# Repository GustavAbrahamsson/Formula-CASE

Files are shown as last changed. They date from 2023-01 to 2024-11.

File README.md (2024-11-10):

# Formula-CASE | Miniature Formula-style RC cars!

## ESP32-S3, FreeRTOS, 4WD
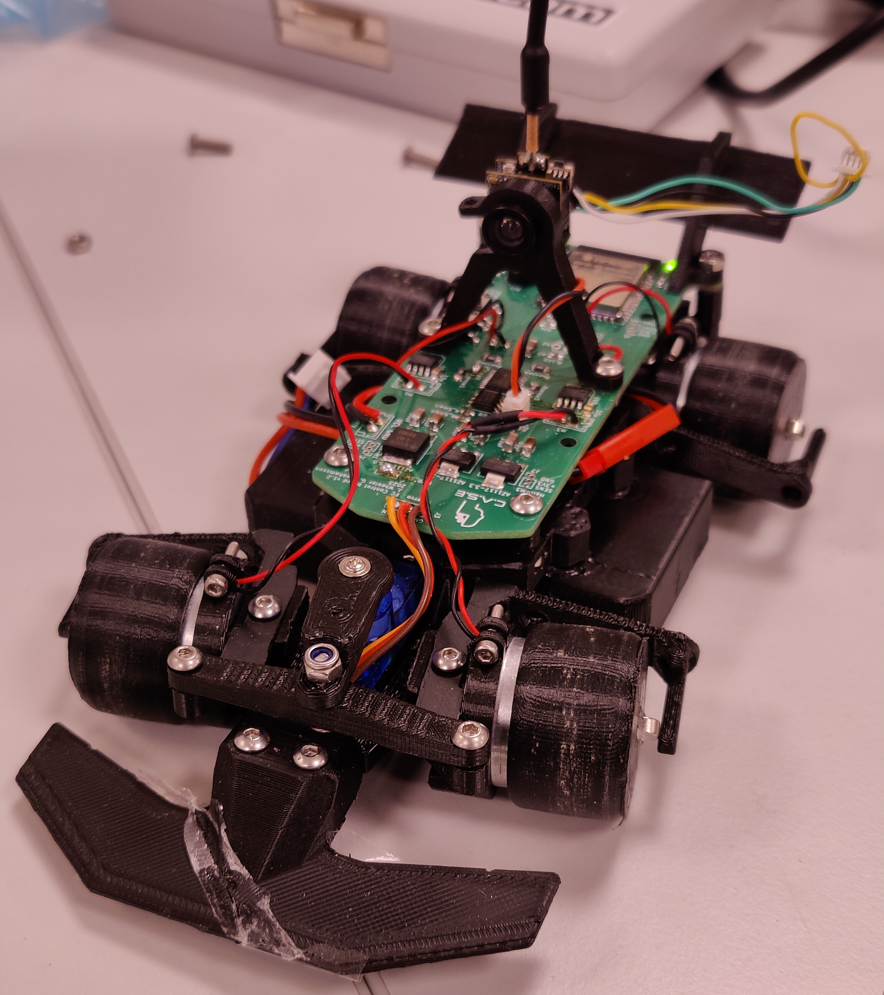
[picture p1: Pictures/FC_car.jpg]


## F1-inspired custom steering wheel, with magnetic paddle shifters


## Remote control with "driver POV" video feed


## PCB
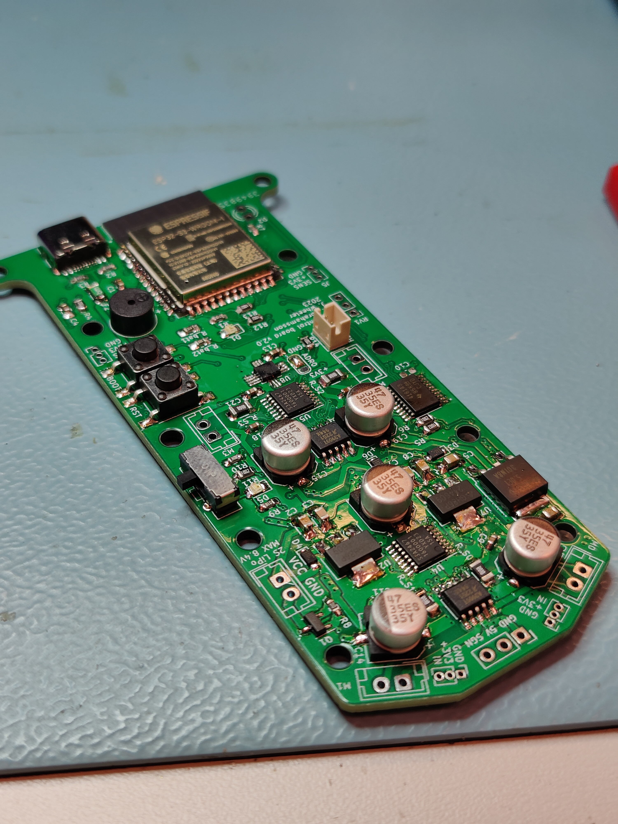
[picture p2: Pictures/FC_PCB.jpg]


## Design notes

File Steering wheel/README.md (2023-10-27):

# FC_Wheel PCB
## v1.0
### Issues:
- The pads for the ESP32-S3 footprint are too small 
- The ESP receives 2.4V even though the LDO outputs 3.3V
  - Use larger vias
- The BOOT and RESET push-buttons need to be more accessable and easier to press
  - Use 'longer' push-buttons with the same footprint
- The battery pins need labels
- The holes are not aligned for the MPU6050 footprint
- Cables
  - Move to a single PCB with no cables

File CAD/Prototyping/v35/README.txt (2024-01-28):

4 x Motor mount
6 x PCB_offset
2 x Rear_PCB_offset
2 x Wheel frame
2 x Wheel frame (mirrored)

1 x Everything else

Note:
2 x PCB_offset could also work

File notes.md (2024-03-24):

# Notes for FC-CONTROL_BOARD

## Hardware notes
### FC Control board v0.1
#### Known faults
- [ ] Wrong 3.3v regulator pinout ordered. Footprint is correct but non standard part was ordered.
- [ ] 5v from USB goes directly to regulated 5v rail (can lead to excessive current draw from/to USB). Should be separate or have reverse current protection.
- [ ] Servo pin header had wrong pinout. Should be 5v, GND, signal. Not signal, 5v, GND.
- [ ] Negative battery terminal is not connected.
- [ ] Silkscreen needs to be improved.
  - [ ] Add pinout for servo header.
  - [ ] Add pinout for battery header.
  - [ ] Label for Reset and Boot buttons needs to be fixed.
- [ ] Screw hole is under the USB connector. Connector should be moved to the side.
- [ ] Components at the back block mounting of back wing.

#### Improvements
- [ ] Improve Voltage/Current protection for USB and battery.
- [ ] Add connector with more GPIO pins for future expansion.
- [ ] Test opamp circuit for halleffect encoder. Implement on pcb if works well.
- [ ] 3.3v and 5v routing is not well done, can be improved.
## MAC address
Mac address for the board can be gotten by using `env:print-mac` and reading serial output.
```
- FC Control board v0.1: 34:85:18:5C:4E:F0
```

### FC Control board v1.1
#### Addressed issues
- [x] Changed footprint for the ESP32-S3 (easier to solder)
- [x] Servo pin header switched to GND, 5V, signal
- [x] Negative battery terminal is not connected.
- [x] Silkscreen needs to be improved. (sort of)
  - [x] Add pinout for battery header.
  - [x] Add pinout for servo header.
  - [x] Label for Reset and Boot buttons needs to be fixed.
- [x] Screw hole is under the USB connector. Connector should be moved to the side.
- [x] Components at the back block mounting of back wing.
#### Additional features
- [x] Added a buzzer
#### What's left
  - [ ] 5v from USB goes directly to regulated 5v rail (can lead to excessive current draw from/to USB). Should be separate or have reverse current protection.
  - [ ] Improve Voltage/Current protection for USB and battery.
  - [ ] Add connector with more GPIO pins for future expansion.
  - [ ] Test opamp circuit for halleffect encoder. Implement on pcb if works well.
  - [ ] 3.3v and 5v routing is not well done, can be improved.
  - [ ] Add connector for the camera
  - [ ] Add connectors for the hall-effect sensors
  - [ ] Add tail-light LED
  - [ ] Decrease bat_level measurements from reading 3.3V to 3.0V as max battery voltage (ESP32 ADC is shit)
  - [ ] Fix silkscreen text sizing

### FC Control board v1.2
#### Addressed issues
  - [x] Add connector for the camera
  - [x] Add connectors for the hall-effect sensors (https://www.mouser.se/ProductDetail/Texas-Instruments/DRV5056A2QLPGM?qs=vdi0iO8H4N3IxI89EIhQ7w%3D%3D Are tested and give a [0.1, 1.1]V range to ADC)
  - [x] Decrease bat_level measurements from reading 3.3V to 3.0V as max battery voltage (ESP32 ADC is shit)
  - [x] Fix silkscreen text sizing

#### Additional features
  - [x] Add tail-light LED

#### Improvements
  - [ ] Add IMU
  - [ ] Fix button footprints
  - [ ] Add reverse current diodes for LDOs
  - [ ] Add small switch with MOSFET to connect/disconnect battery
  - [ ] Change motor drivers
  - [ ] Add fuse for USB
  - [ ] Add undervoltage protection for the battery

### FC Control board v1.3 [WIP]
#### Addressed issues
  - [x] Add IMU
  - [x] Fix button footprints
  - [x] Add reverse current diodes for LDOs
  - [x] Add small switch with MOSFET to connect/disconnect battery
  - [x] Change motor drivers
  - [x] Add fuse for USB

#### Improvements

### Hall effect sensor things (Johan)
- DRV5056
  - Unipolar, has been used for the first prototypes.
  - A2 sensitivity gives 0.1 - 0.9 v centered at 0.6v when measuring from outside of wheel.
    - This is how Johan tested during christmas break.
      - Was then driven at 3.3 v?
    - A2 has 100 mv/mT at 5 V, 39 mT range
    - If a bipolar sensor is used, then a larger gain can be used without problems since saturation is not a problem in the same way. (0.1 v is the lowest value that can be outputted)
      - 39 * 0.5/3.3 = 5.9 mT
- DRV5055
  - Bipolar, has not been used yet.
  - A1 has $\pm$ 21 mT range
    - Buy 2 for "outside wheel measurements"
      - 15 mm distance from magnet to sensor
  - Inside wheel measurements
    - ~ 5 mm distance from magnet to sensor
    - 1/3 of the distance
    - Field strength is $\propto 1/r^3$
    - $\frac{1/5^3}{1/15^3} = 3^3 = 27$
    - This could give ~ $27 \cdot 5.9 = 160$ mT
    - A4 has $\pm$ 169 mT range
      - Buy 2 for "inside wheel measurements"
- [TMAG5273](https://www.ti.com/lit/ds/symlink/tmag5273.pdf?ts=1708821180315)
  - I2C
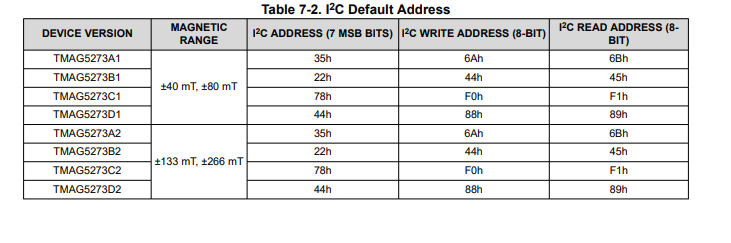
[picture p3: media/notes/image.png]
  
  - A,B,C,D have different addresses
  - 1 or 2 has different sensitivity
    - Buy 2 of each range for testing with different addresses
      - A1, B1, C2, D2
      - These are not all in stock at mouser...
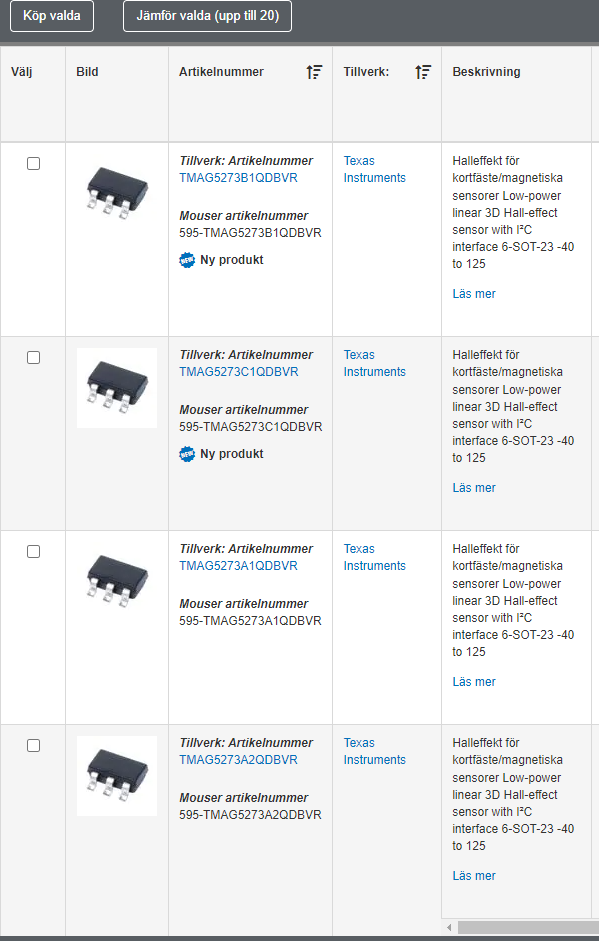
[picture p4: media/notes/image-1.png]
      - 
        - Buy one of each
- MLX90393
  - Used in foot sensor project

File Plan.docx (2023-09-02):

# Car

- 4WD
  - 4 x 3-12V, 1730RPM https://www.amazon.se/gp/product/B088GMRP26/ref=ppx_yo_dt_b_asin_title_o05_s00?ie=UTF8&psc=1
- Steering
  - SG-90
- Radio control
  - NRF24L01?
- FPV
  - Separate cam + screen
    - 5.8 GHz?
- 2S 850 mAh LiPo
  - Hålls fast på undersidan av gummiband/kardborreband
  - JST-connector?
  - Till PCB: VCC, GND

## PCB

Anslutningar:

- VCC, GND från batteri
- 4 x motoranslutningar
  - 2 pins, motorA, motorB
- SG90-servo till styrning
  - 3 pins, 5V (3V?), GND, SIGNAL (PWM)
- Strömförsörjning till kamera+sändare
  - Spänning? 7.4V direkt från batteri?
- USB-C
  - Kopplad till ESP32 för uppladdning av kod etc

Komponenter:

- ESP32
- 4 x motordrivare
- 4 x strömsensorer till varje motor
  - I2C?
- 4 x hall-effect sensor till varje hjul
  - 4 x ADC

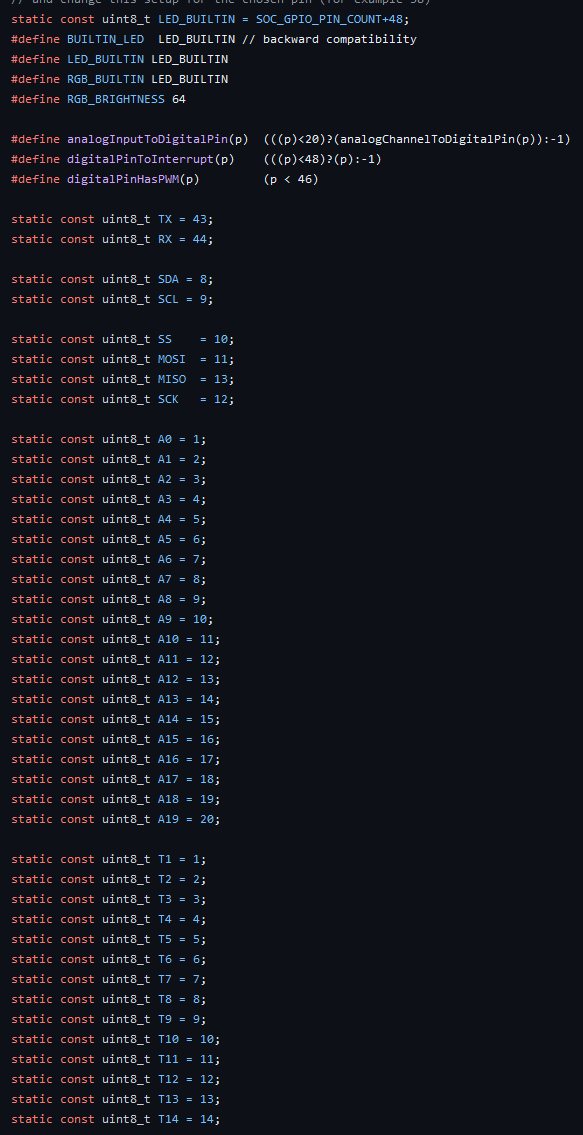
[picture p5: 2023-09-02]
Electronics/PCB/ESP32-S3.png

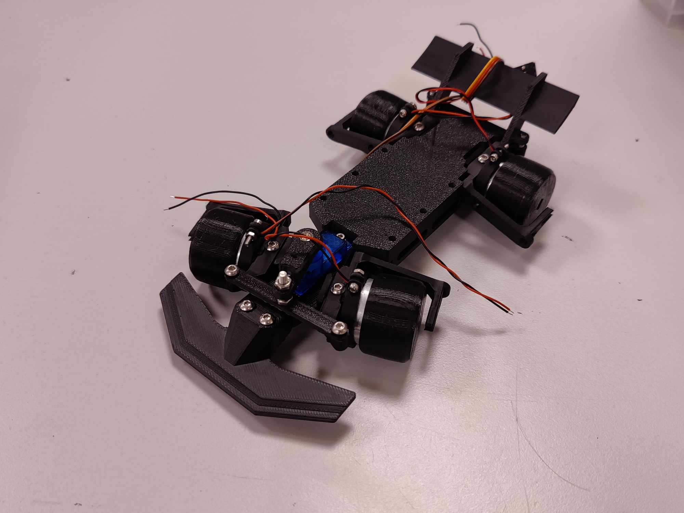
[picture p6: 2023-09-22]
Pictures/Prototype4.jpg

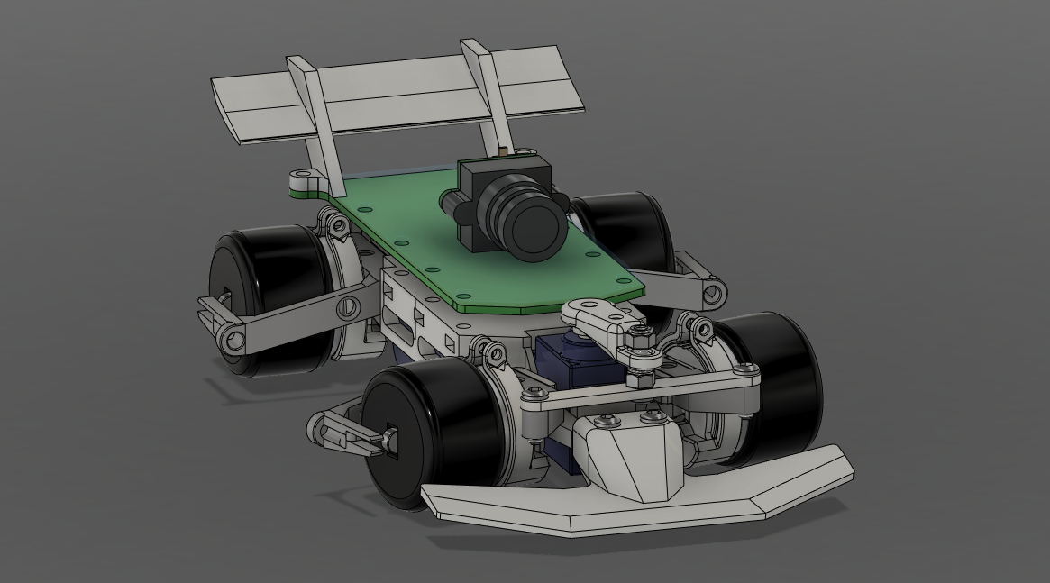
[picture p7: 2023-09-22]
Pictures/FC-CAD_prototype4.png

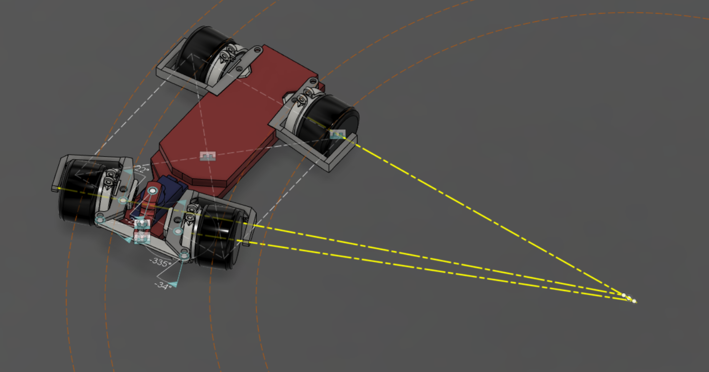
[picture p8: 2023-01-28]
CAD/radius2.PNG

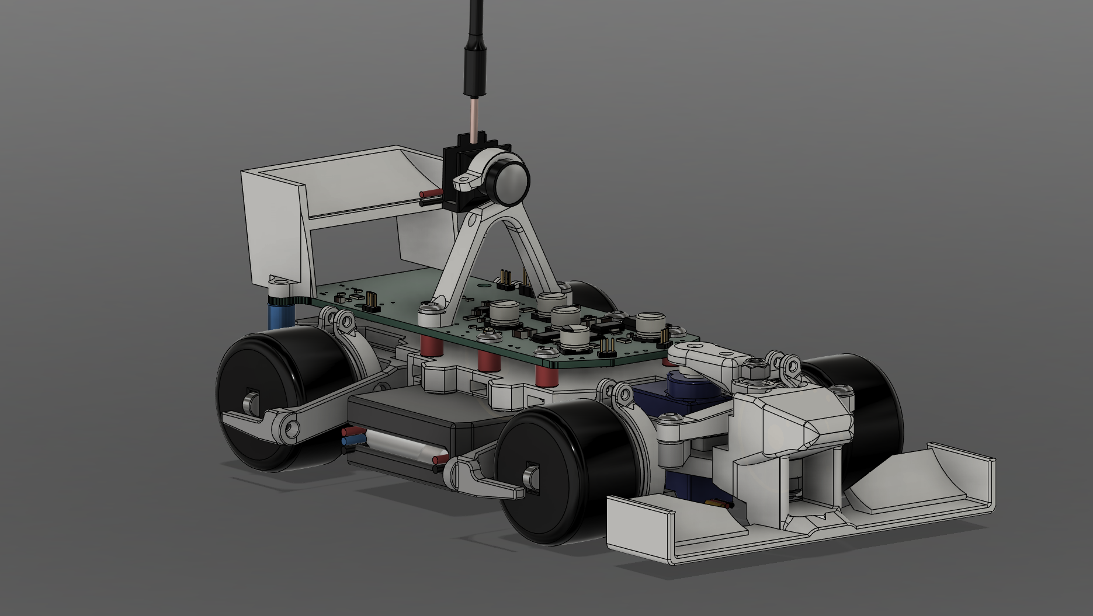
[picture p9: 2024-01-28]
CAD/Prototyping/v35/v35.png

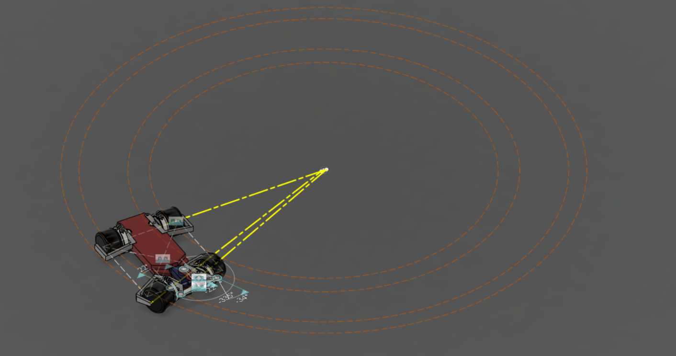
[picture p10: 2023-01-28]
CAD/radius.PNG

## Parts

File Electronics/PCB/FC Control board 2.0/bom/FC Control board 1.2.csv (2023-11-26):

Id | Designator | Footprint | Quantity | Designation | Supplier and ref
1 | C7,C8,C5,C3,C6,C2 | C_1206_3216Metric | 6 | 10uF
2 | M1,M3,M2,M4 | JST_EH_B2B-EH-A_1x02_P2.50mm_Vertical | 4 | Motor_DC_ALT
3 | C1 | C_1206_3216Metric | 1 | C
4 | C4 | C_0805_2012Metric_Pad1.18x1.45mm_HandSolder | 1 | 100n
5 | C13,C12,C14,C11 | C_0805_2012Metric_Pad1.18x1.45mm_HandSolder | 4 | 10µ
6 | U7,U2 | SOT-223-3_TabPin2 | 2 | AZ1117-3.3
7 | J6 | PinHeader_1x03_P1.27mm_Vertical | 1 | Hall-M4
8 | U3 | TO-252-2 | 1 | AZ1117-5.0
9 | R2,R3 | R_0805_2012Metric_Pad1.20x1.40mm_HandSolder | 2 | 5.1K
10 | D1 | LED_0805_2012Metric_Pad1.15x1.40mm_HandSolder | 1 | PWR_LED
11 | U9 | SOIC-8-1EP_3.9x4.9mm_P1.27mm_EP2.514x3.2mm | 1 | LM358_DFN
12 | R7,R1 | R_0805_2012Metric_Pad1.20x1.40mm_HandSolder | 2 | R_LED
13 | RV1 | PinHeader_1x03_P2.00mm_Vertical | 1 | R_Potentiometer_Small
14 | U6 | SOP65P640X120-20N | 1 | INA4181A3IPWR
15 | J2 | JST-ZH-2_PIN | 1 | CAM
16 | R4 | R_0805_2012Metric_Pad1.20x1.40mm_HandSolder | 1 | 10K
17 | SW3 | PinHeader_1x02_P2.00mm_Vertical | 1 | PWR_SW
18 | U10,U5,U11,U8 | ZXBM5210 | 4 | ZXBM5210
19 | SW2 | SW_Push_1P1T_NO_6x6mm_H9.5mm | 1 | BOOT
20 | J7 | PinHeader_1x03_P1.27mm_Vertical | 1 | Hall-M3
21 | BZ1 | MagneticBuzzer_Kobitone_254-EMB73-RO | 1 | AC-703R-P4
22 | Rsense1,Rsense2,Rsense3,Rsense4 | R_1206_3216Metric | 4 | R_Small
23 | R_bat1 | R_0805_2012Metric_Pad1.20x1.40mm_HandSolder | 1 | 90k
24 | U1 | ESP32-S3-WROOM-1 | 1 | ESP32-S3-WROOM-1-N8
25 | J1 | USB_C_Receptacle_HRO_TYPE-C-31-M-12 | 1 | USB_C_Receptacle_USB2.0
26 | R6,R5 | R_0603_1608Metric_Pad0.98x0.95mm_HandSolder | 2 | R_Small
27 | C10 | C_0603_1608Metric | 1 | C_Small
28 | SW1 | SW_Push_1P1T_NO_6x6mm_H9.5mm | 1 | RST
29 | BT1 | JST_EH_B2B-EH-A_1x02_P2.50mm_Vertical | 1 | Battery
30 | J5 | PinHeader_1x03_P1.27mm_Vertical | 1 | Hall-M2
31 | J3 | PinSocket_1x03_P2.54mm_Vertical | 1 | Servo
32 | D2 | LED_D3.0mm | 1 | RED
33 | J4 | PinHeader_1x03_P1.27mm_Vertical | 1 | Hall-M1
34 | R_bat2 | R_0805_2012Metric_Pad1.20x1.40mm_HandSolder | 1 | 50k
35 | JP1 | SolderJumper-3_P1.3mm_Bridged12_RoundedPad1.0x1.5mm | 1 | SolderJumper_3_Bridged12

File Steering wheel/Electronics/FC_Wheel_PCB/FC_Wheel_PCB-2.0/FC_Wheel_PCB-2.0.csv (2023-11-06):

Id | Designator | Footprint | Quantity | Designation | Supplier and ref
1 | Volume1 | Potentiometer_ACP_CA9-H3,8_Horizontal | 1 | R_Buzzer
2 | BZ1 | Buzzer_12x9.5RM7.6 | 1 | Buzzer1
3 | C7,C9,C6,C5 | C_1206_3216Metric | 4 | 10uF
4 | C2 | C_1206_3216Metric | 1 | C
5 | PADDLE2 | PinHeader_1x02_P2.54mm_Vertical | 1 | SW_L
6 | R12,R11 | R_0805_2012Metric_Pad1.20x1.40mm_HandSolder | 2 | 5.1K
7 | J7 | PinHeader_1x06_P2.54mm_Vertical | 1 | LED_Driver
8 | BTN1 | SPST_PushButton_Cyl | 1 | SW_BTN1
9 | BTN3 | SPST_PushButton_Cyl | 1 | SW_BTN3
10 | BZ2 | Buzzer_12x9.5RM7.6 | 1 | Buzzer2
11 | J1 | USB_C_Receptacle_HRO_TYPE-C-31-M-12 | 1 | USB_C
12 | BTN4 | SPST_PushButton_Cyl | 1 | SW_BTN4
13 | J2 | PinHeader_1x08_P2.54mm_Vertical | 1 | Display_con
14 | U2 | ESP32-S3-WROOM-1_handsolder | 1 | ESP32-S3-WROOM-1-N8
15 | BT1 | 1043_fromMouser | 1 | Battery
16 | R1,R10,R2 | R_0805_2012Metric_Pad1.20x1.40mm_HandSolder | 3 | 10K
17 | R_bat1 | R_0805_2012Metric_Pad1.20x1.40mm_HandSolder | 1 | 50k
18 | U6,U7 | SOT-223-3_TabPin2 | 2 | AZ1117-3.3
19 | R9 | R_0805_2012Metric_Pad1.20x1.40mm_HandSolder | 1 | R_LED
20 | BTN2 | SPST_PushButton_Cyl | 1 | SW_BTN2
21 | C8 | C_0805_2012Metric_Pad1.18x1.45mm_HandSolder | 1 | 100n
22 | SW3 | STST Switch 2MS6T1B3M2QES | 1 | BATTERY_SW
23 | PADDLE1 | PinHeader_1x02_P2.54mm_Vertical | 1 | SW_R
24 | SW10 | RotaryEncoder_Alps_EC12E-Switch_Vertical_H20mm | 1 | RotaryEncoder
25 | R_bat2 | R_0805_2012Metric_Pad1.20x1.40mm_HandSolder | 1 | 125k
26 | D1 | LED_D5.0mm | 1 | PWR_LED
27 | J5 | PinHeader_1x03_P2.54mm_Vertical | 1 | R_TRIGGER
28 | J4 | PinHeader_1x03_P2.54mm_Vertical | 1 | L_TRIGGER
29 | J3 | PinHeader_1x08_P2.54mm_Vertical | 1 | MPU6050_con
30 | S3,S1 | TL3336AF160Q | 2 | TL3336AF160Q
31 | J6 | PinHeader_1x07_P2.54mm_Vertical | 1 | Pinout

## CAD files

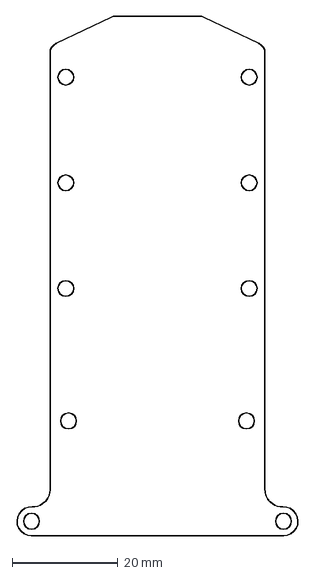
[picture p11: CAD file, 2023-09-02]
CAD/DXF/PCB-outline.dxf
53.5 x 98.4 mm

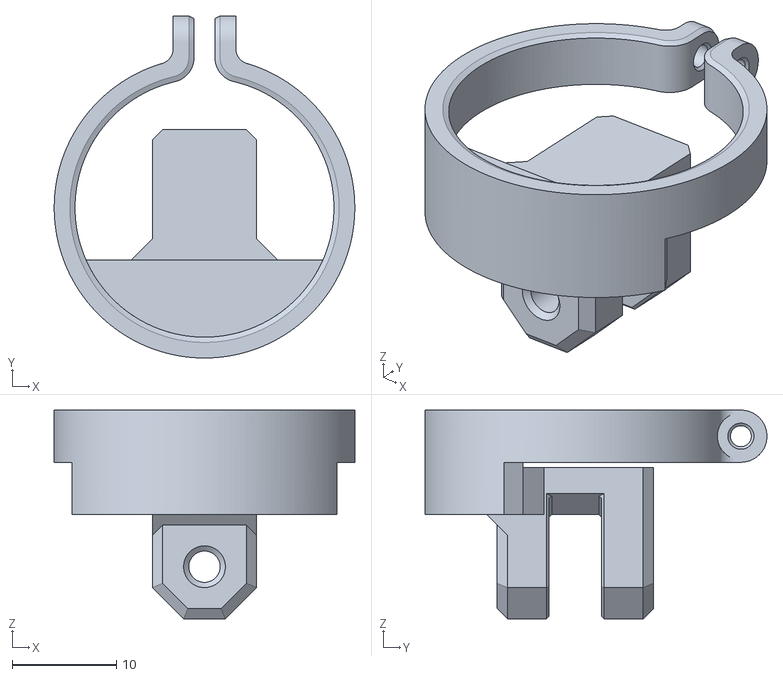
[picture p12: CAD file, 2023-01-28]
CAD/Prototyping/Motor mount/Motor mount.stl
28.8 x 32.8 x 20.0

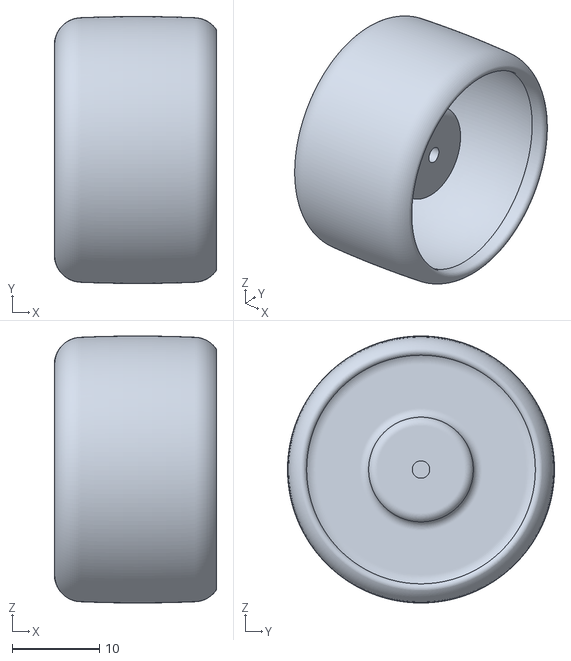
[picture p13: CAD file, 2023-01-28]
CAD/Prototyping/Tyres/Back wheel v1.stl
18.6 x 30.6 x 30.6

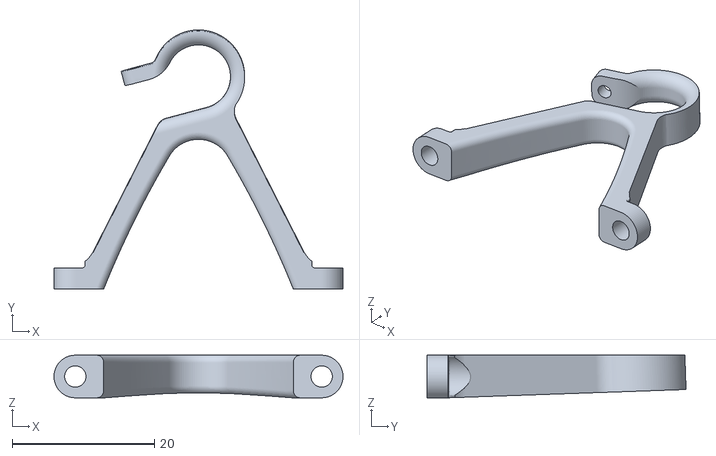
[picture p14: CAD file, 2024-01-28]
CAD/Prototyping/v35/Camera mount TX06_-2.stl
40.7 x 36.5 x 6.00

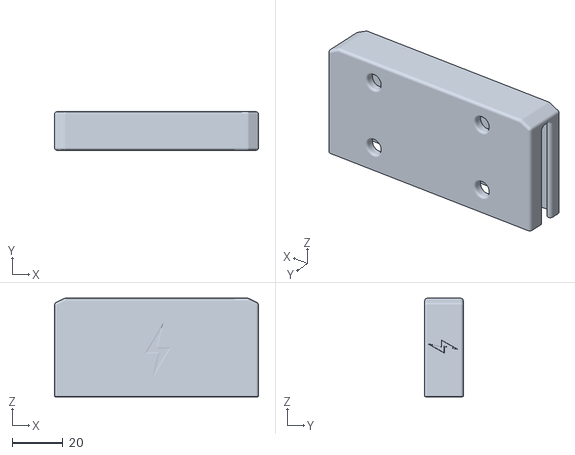
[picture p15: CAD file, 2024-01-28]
CAD/Prototyping/v35/Print/Battery Lid v2.stl
80.1 x 15.2 x 38.7

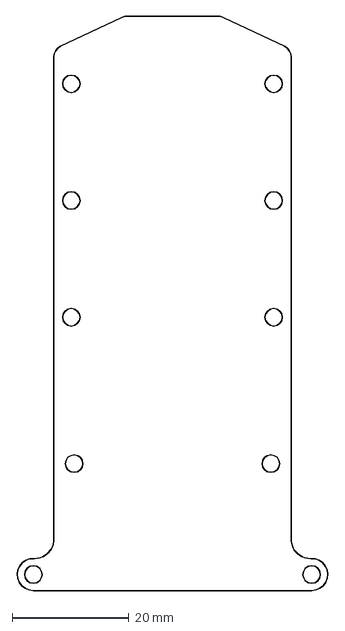
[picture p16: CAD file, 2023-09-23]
Electronics/PCB/DXF/PCB_outline_prototype4.dxf
53.5 x 98.4 mm

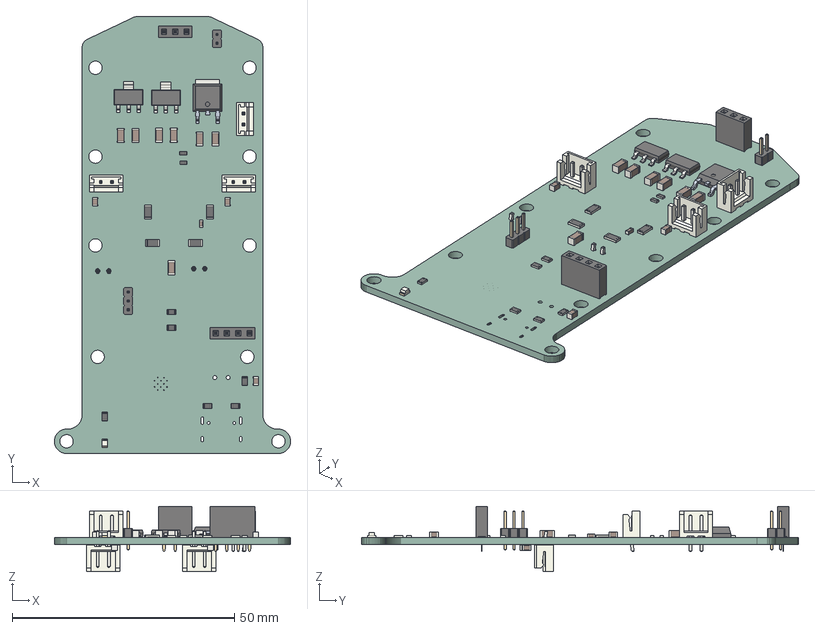
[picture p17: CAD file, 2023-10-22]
Electronics/PCB/FC Control board 1.1/FC Control board 1.1.step
53.2 x 98.4 x 14.7 mm
FC Control board 1.1 PCB

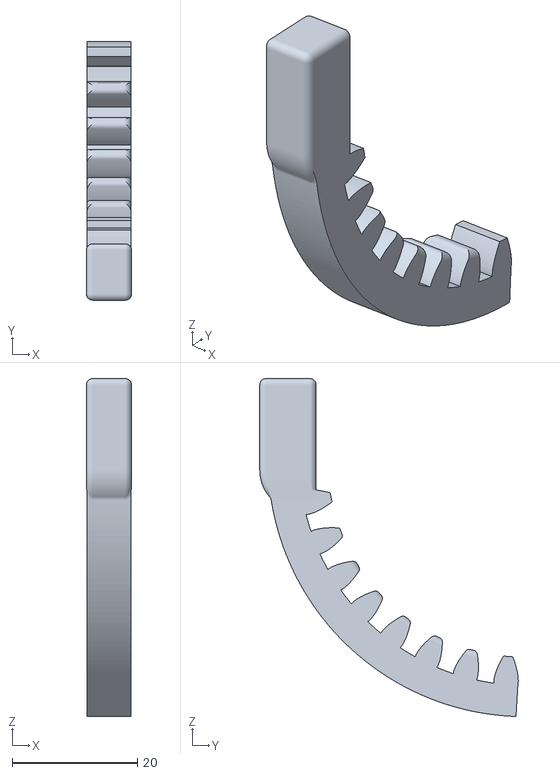
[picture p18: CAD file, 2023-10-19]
Steering wheel/CAD/Analog trigger/Analog trigger v27/Cog_trigger.stl
7.20 x 41.3 x 53.9

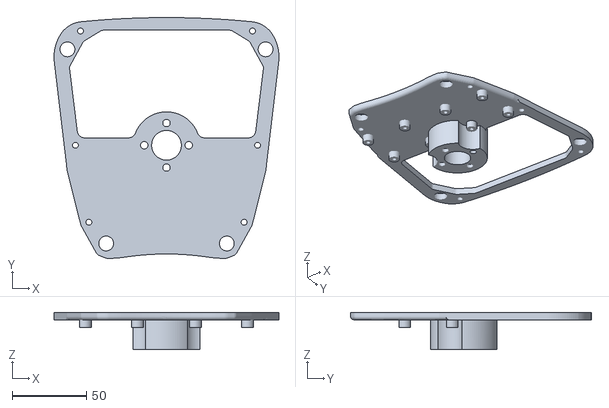
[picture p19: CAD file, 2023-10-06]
Steering wheel/CAD/Back plate/Back plate v25/Back plate.stl
151.6 x 162.3 x 25.0

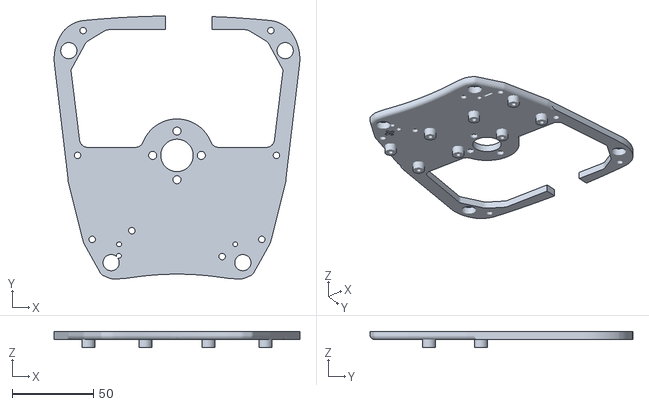
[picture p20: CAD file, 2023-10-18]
Steering wheel/CAD/Back plate/Back plate v36.stl
151.6 x 162.2 x 10.2

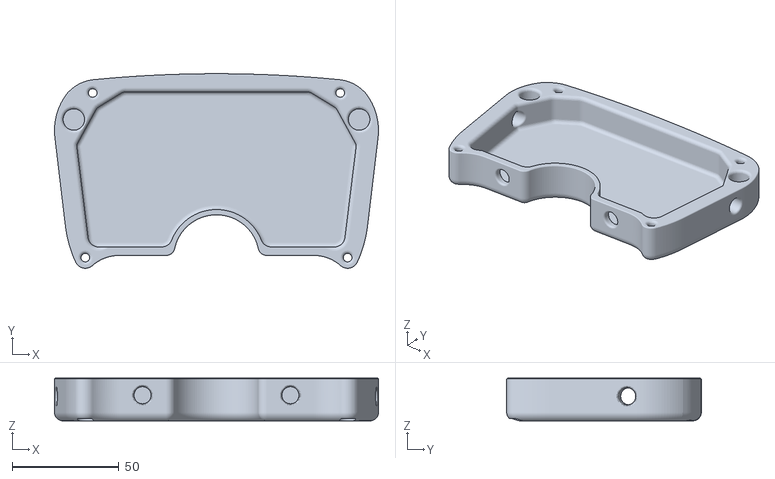
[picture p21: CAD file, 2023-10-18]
Steering wheel/CAD/Cover/Cover v40.stl
151.6 x 91.0 x 20.0

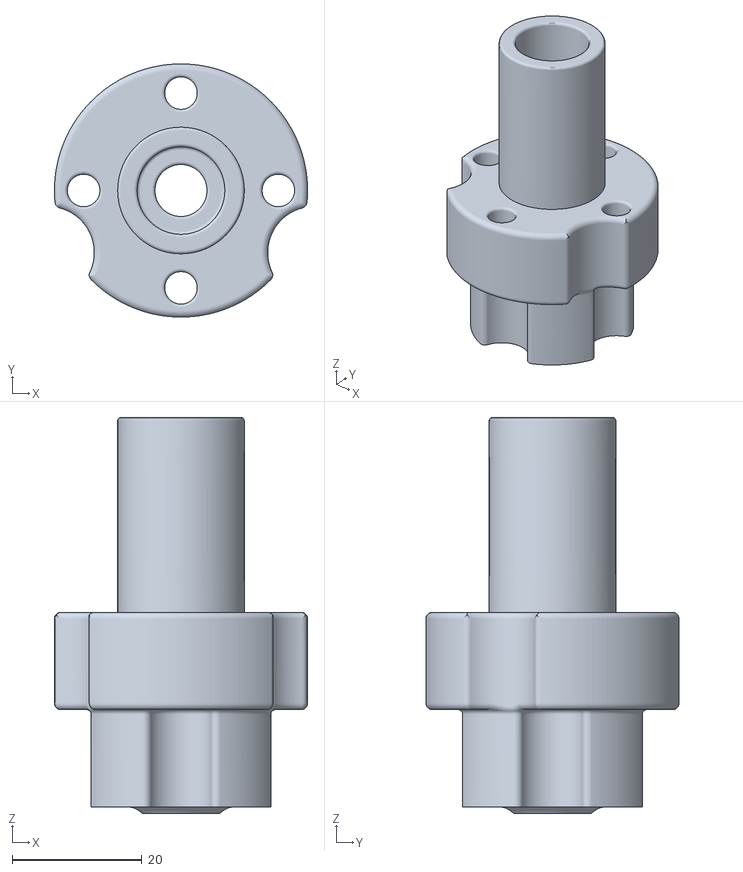
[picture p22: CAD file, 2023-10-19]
Steering wheel/CAD/Docking station/Docking rotor/Docking rotor v44/Docking_rotor.stl
39.0 x 39.0 x 61.0

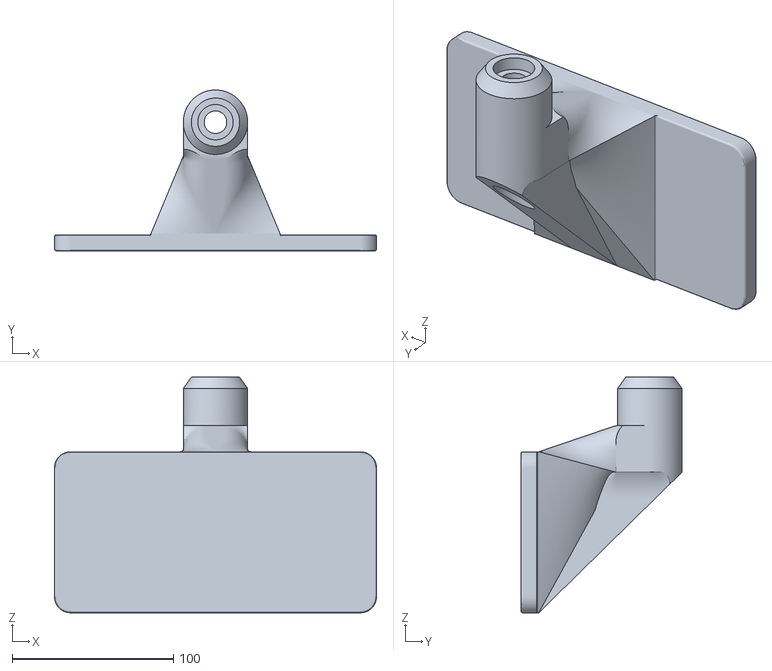
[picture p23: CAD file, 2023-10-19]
Steering wheel/CAD/Docking station/Docking stator/Docking stator v44/Docking_stator.stl
200.0 x 100.0 x 146.4

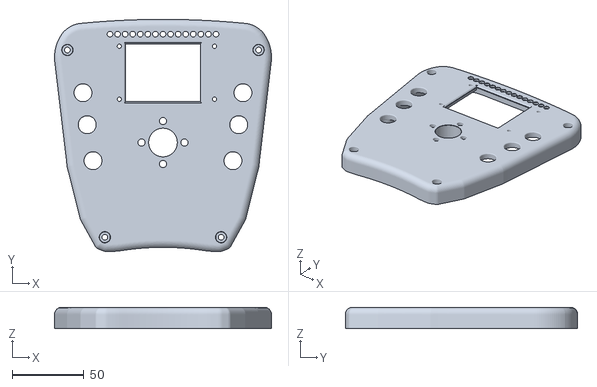
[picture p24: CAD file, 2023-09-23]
Steering wheel/CAD/Front dash/Front dash v21/Front dash v21.stl
151.6 x 162.3 x 15.0

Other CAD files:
Steering wheel/CAD/Front dash/Front dash v34.stl
Steering wheel/CAD/Handles v24/RightFrontHandle.stl
Steering wheel/CAD/SLS print racerbil/Handles v24/RightBackHandle.stl
Steering wheel/CAD/Steering_wheel_frame.dxf
CAD/Prototyping/Prototype1/Frame.stl
CAD/Prototyping/Prototype1/Linkage and encoder mount FL.stl
CAD/Prototyping/Prototype1/Linkage and encoder mount FR.stl
CAD/Prototyping/Prototype1/Motor mount.stl
CAD/Prototyping/Prototype1/Steering guider.stl
CAD/Prototyping/Prototype1/Steering linkage.stl
CAD/Prototyping/Prototype2/FC_Prototype2.3mf
CAD/Prototyping/Prototype2/Frame V2.stl
CAD/Prototyping/Prototype2/Motor mount V2.stl
CAD/Prototyping/Prototype2/Steering guider V2.stl
CAD/Prototyping/Prototype2/Steering linkage V2.stl
CAD/Prototyping/Prototype2/Wheel frame V2 L.stl
CAD/Prototyping/Prototype2/Wheel frame V2 R.stl
CAD/Prototyping/Tyres/Back wheel outrunner on motor 2.stl
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

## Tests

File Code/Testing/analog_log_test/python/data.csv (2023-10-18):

micros | voltage | seconds | current | milliampere
12 | 1.10948 | 1.2e-05 | -0.002378971999999993 | -2.378971999999993
912 | 1.10948 | 0.000912 | -0.002378971999999993 | -2.378971999999993
1788 | 1.11437 | 0.001788 | -0.0019090429999999853 | -1.9090429999999854
2728 | 1.11437 | 0.002728 | -0.0019090429999999853 | -1.9090429999999854
3664 | 1.11437 | 0.003664 | -0.0019090429999999853 | -1.9090429999999854
4600 | 1.10948 | 0.0046 | -0.002378971999999993 | -2.378971999999993
5528 | 1.10948 | 0.005528 | -0.002378971999999993 | -2.378971999999993
6456 | 1.10948 | 0.006456 | -0.002378971999999993 | -2.378971999999993
7384 | 1.11437 | 0.007384 | -0.0019090429999999853 | -1.9090429999999854
8320 | 1.11437 | 0.00832 | -0.0019090429999999853 | -1.9090429999999854
9256 | 1.11926 | 0.009256 | -0.0014391140000000052 | -1.4391140000000053
10188 | 1.10948 | 0.010188 | -0.002378971999999993 | -2.378971999999993
11160 | 1.10459 | 0.01116 | -0.002848901000000001 | -2.848901000000001
12128 | 1.11926 | 0.012128 | -0.0014391140000000052 | -1.4391140000000053
13112 | 1.11437 | 0.013112 | -0.0019090429999999853 | -1.9090429999999854
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

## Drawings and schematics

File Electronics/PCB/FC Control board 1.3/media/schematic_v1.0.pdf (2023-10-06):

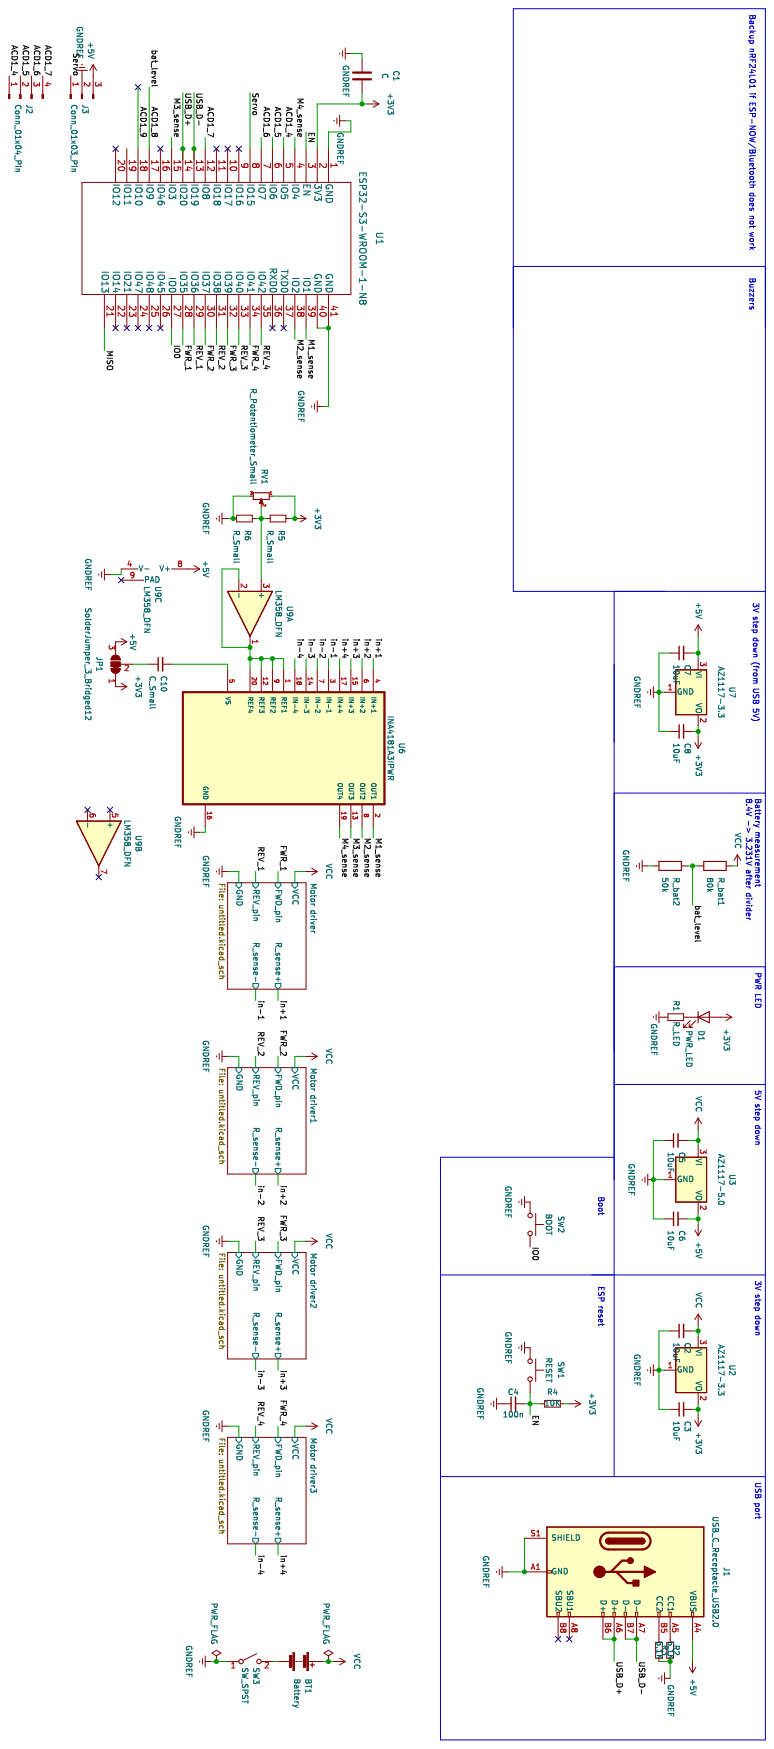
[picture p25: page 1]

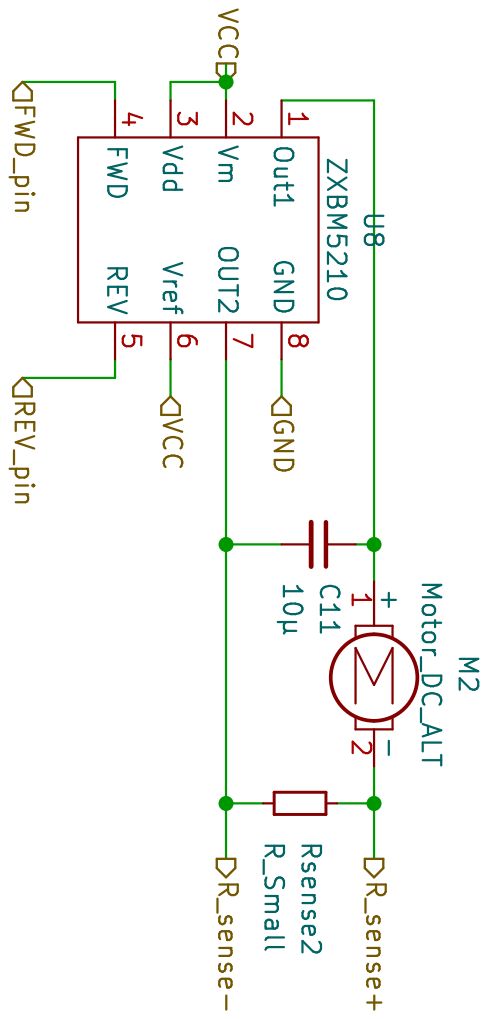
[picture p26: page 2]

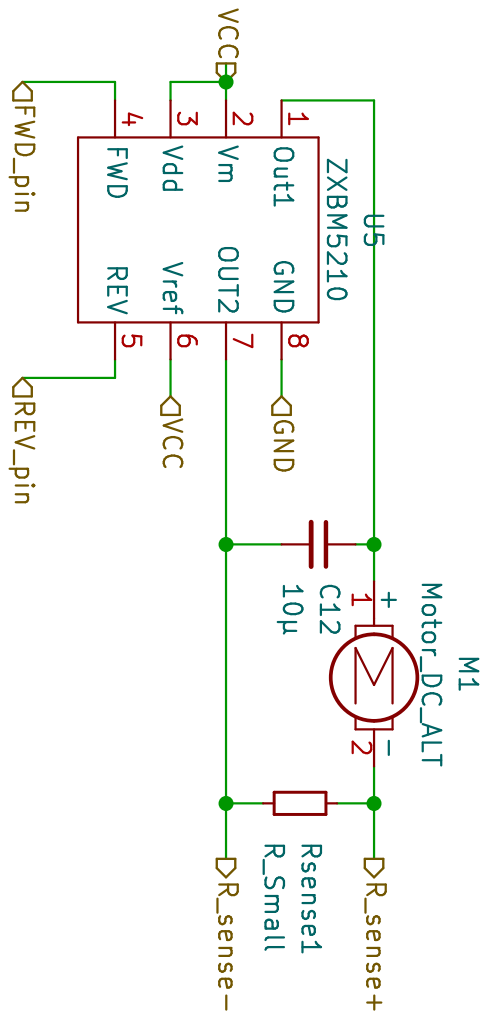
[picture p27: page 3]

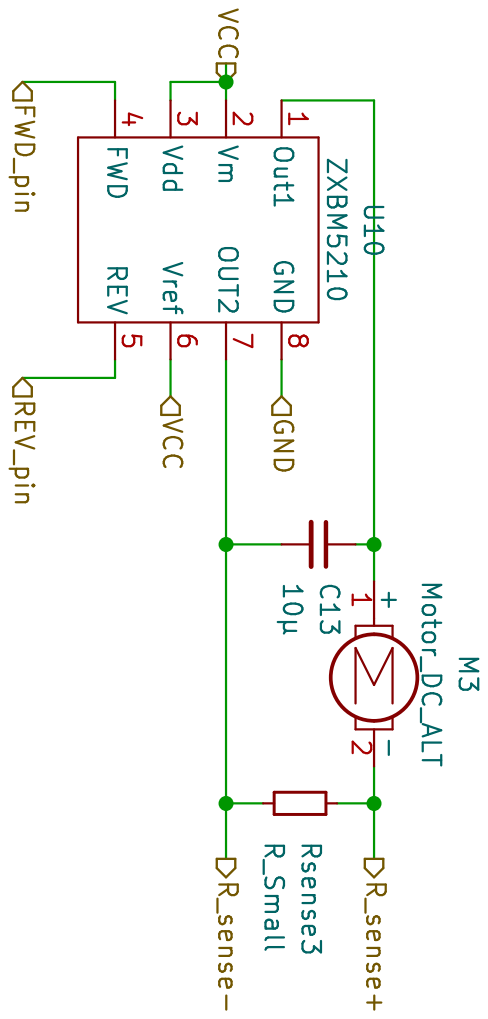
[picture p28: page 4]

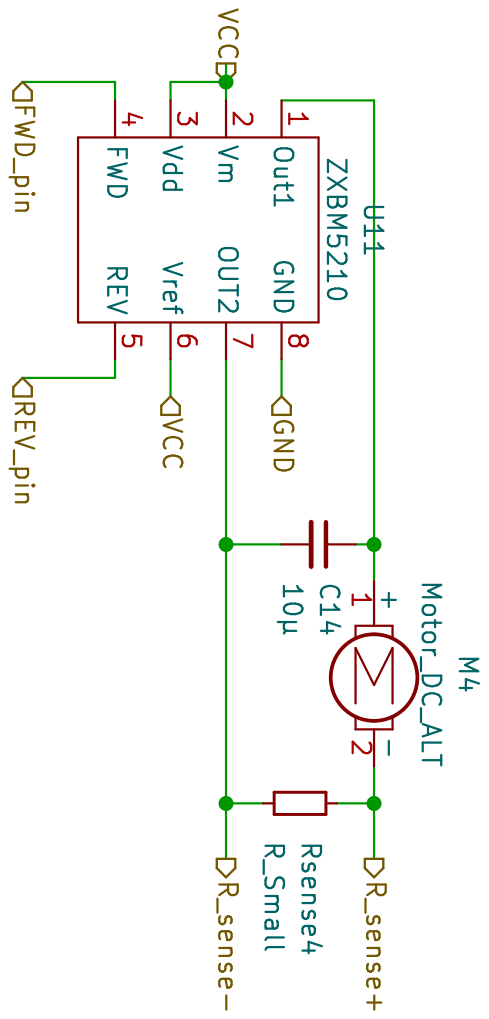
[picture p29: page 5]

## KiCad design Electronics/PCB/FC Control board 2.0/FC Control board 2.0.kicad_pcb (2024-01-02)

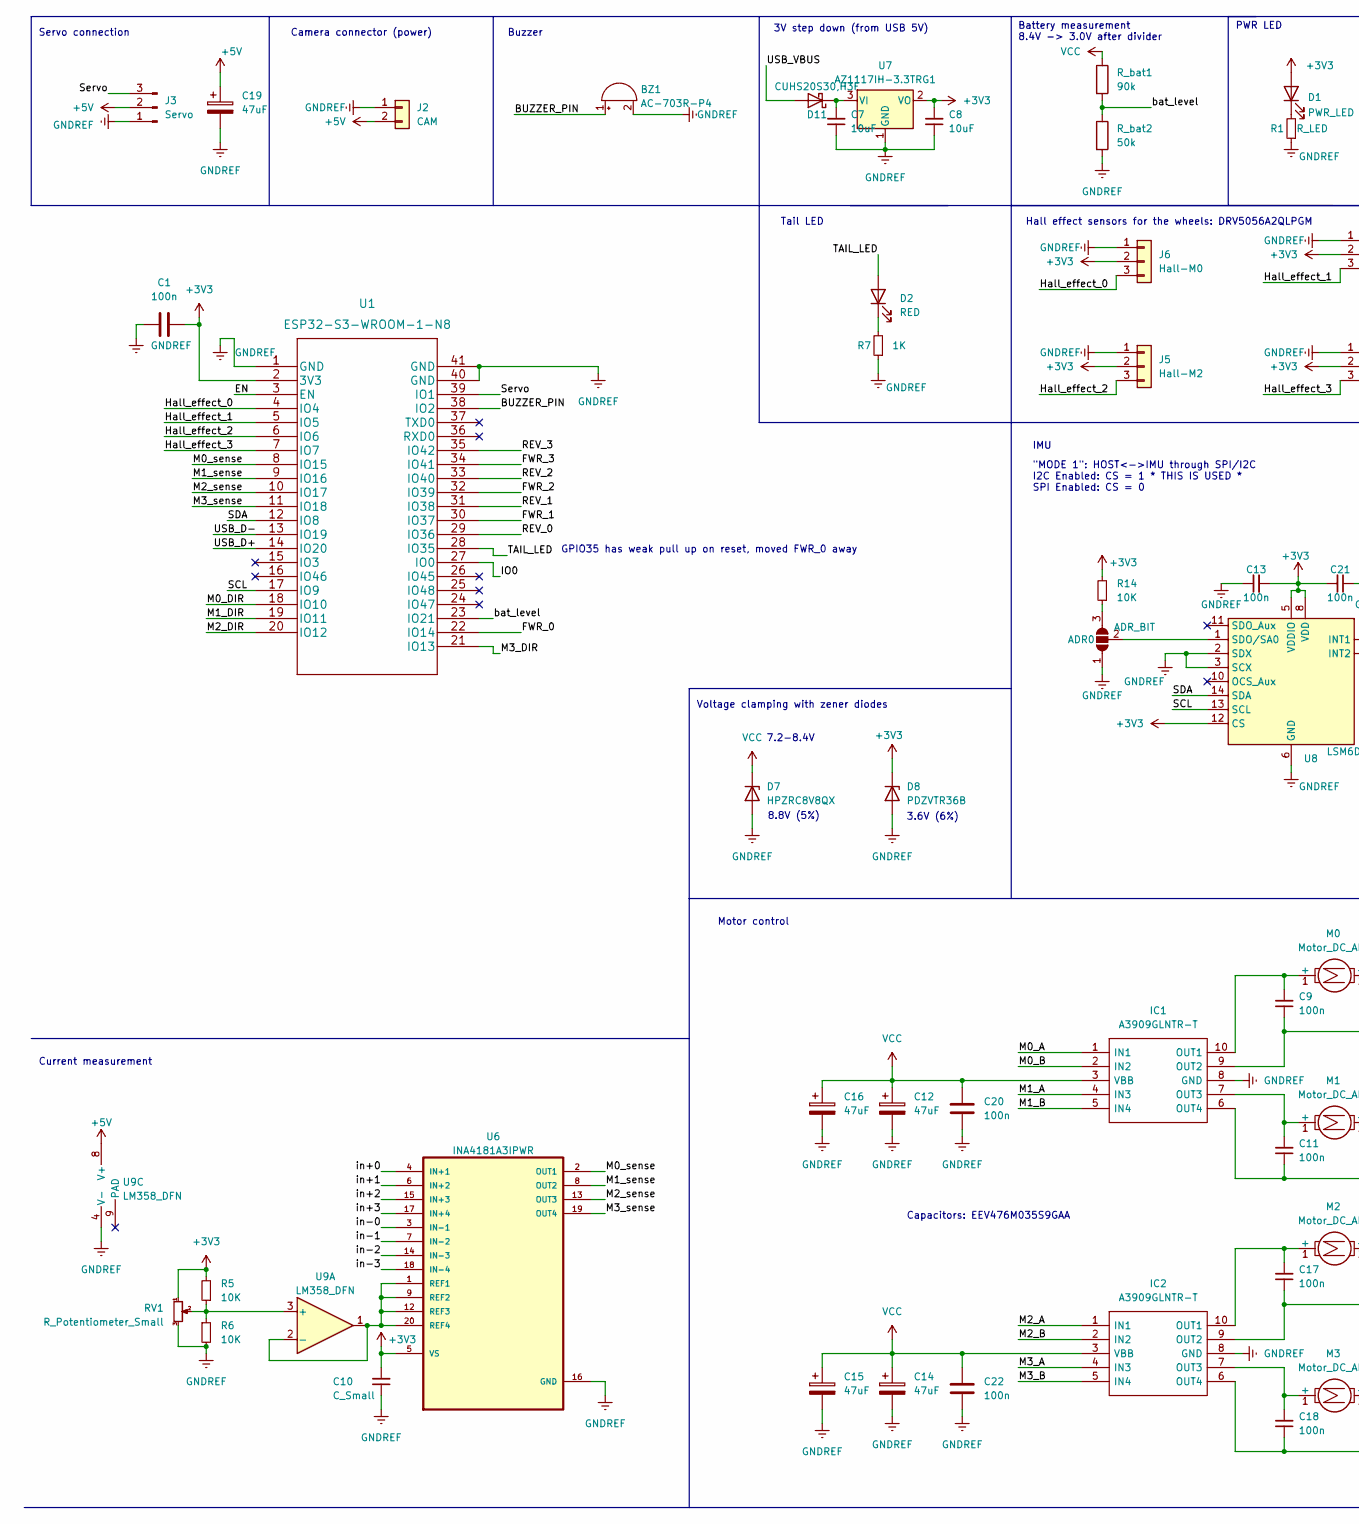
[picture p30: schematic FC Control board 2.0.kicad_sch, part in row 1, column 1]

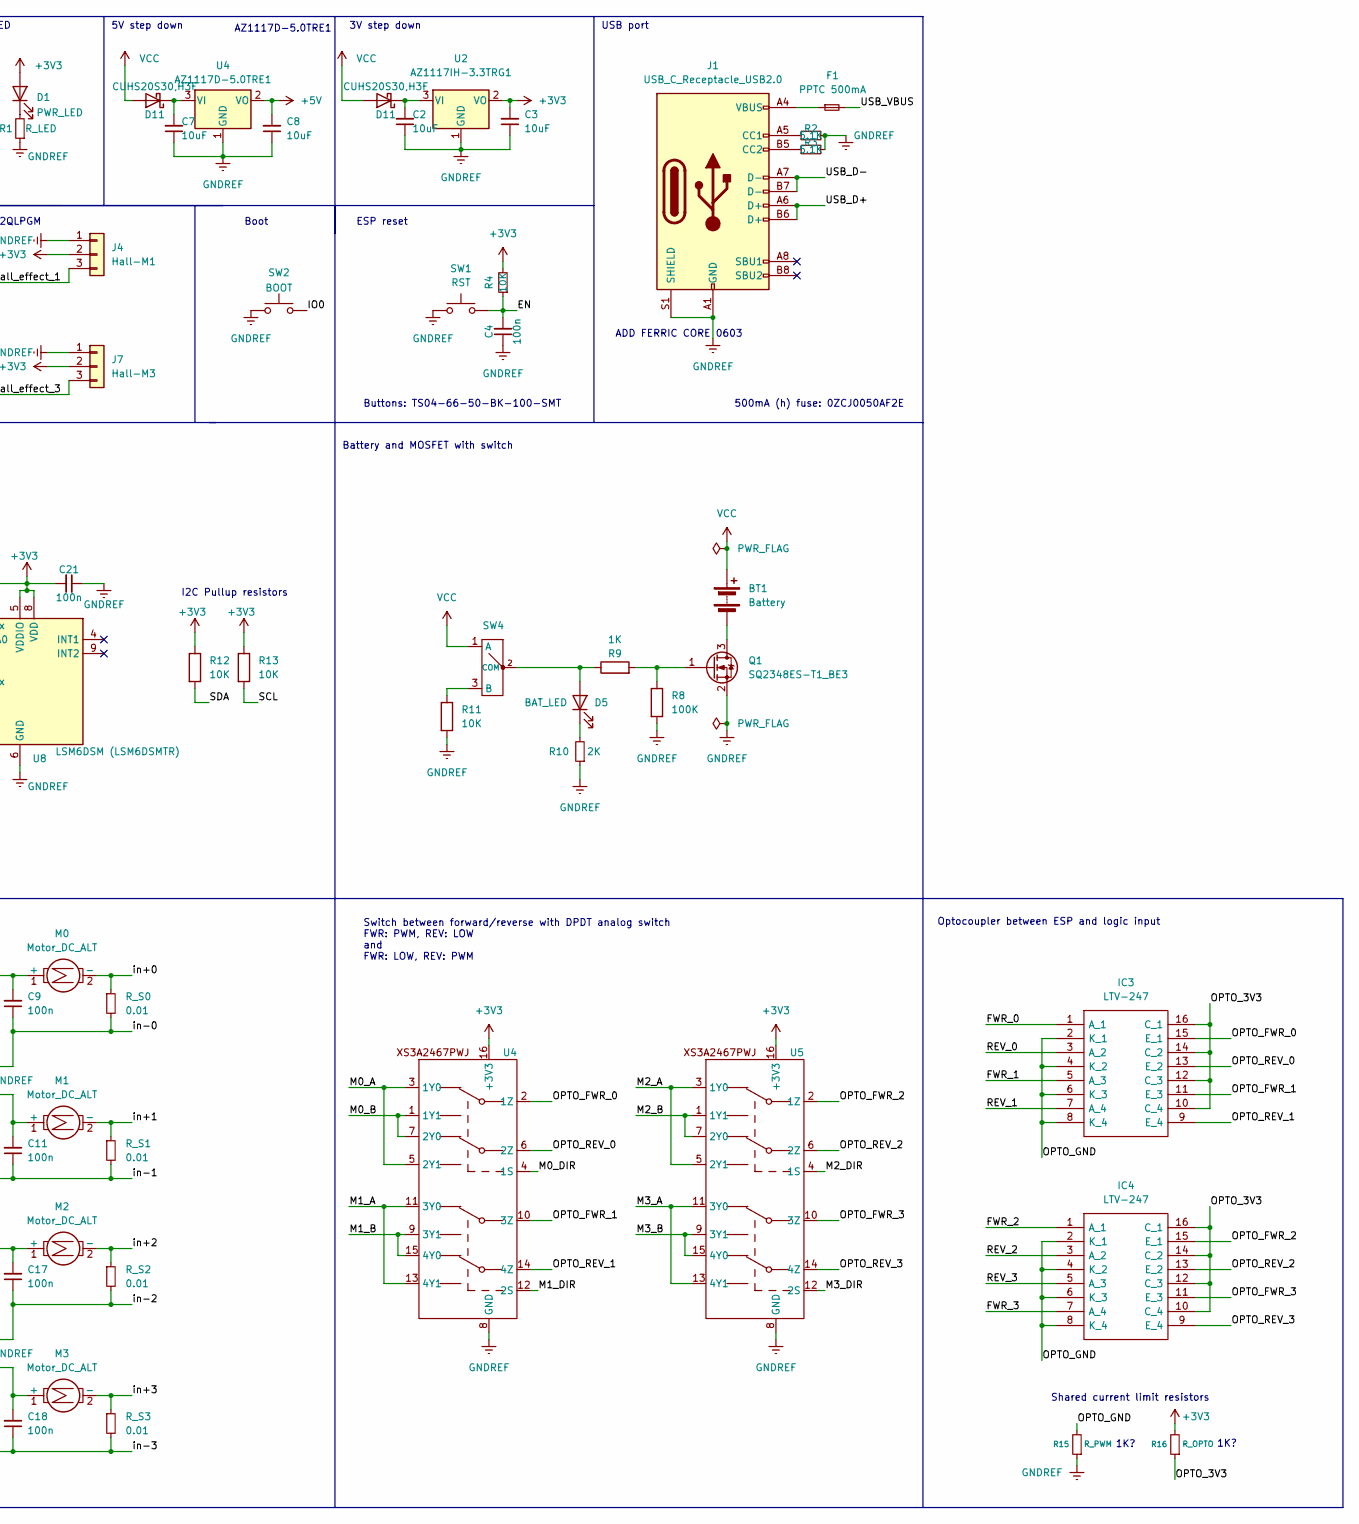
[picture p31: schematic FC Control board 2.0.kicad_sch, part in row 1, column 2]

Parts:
ADR0: ADR_BIT; SolderJumper-3_P1.3mm_Open_RoundedPad1.0x1.5mm_NumberLabels
BT1: Battery; JST_EH_B2B-EH-A_1x02_P2.50mm_Vertical
BZ1: AC-703R-P4; MagneticBuzzer_Kobitone_254-EMB73-RO
C1, C9, C11, C17, C18, C20, C22: 100n; C_0603_1608Metric_Pad1.08x0.95mm_HandSolder
C2, C3, C7, C8: 10uF; C_1206_3216Metric
C4, C13, C21: 100n; C_0805_2012Metric_Pad1.18x1.45mm_HandSolder
C10: C_Small; C_0603_1608Metric
C12, C14, C15, C16, C19: 47uF; CP_Elec_6.3x5.4
D1: PWR_LED; LED_0805_2012Metric_Pad1.15x1.40mm_HandSolder
D2: RED; LED_D3.0mm
D5: BAT_LED; LED_0805_2012Metric_Pad1.15x1.40mm_HandSolder
D7: HPZRC8V8QX
D8: PDZVTR36B
D11: CUHS20S30,H3F
F1: PPTC 500mA; Fuse_1206_3216Metric
IC1, IC2: A3909GLNTR-T; SOP100P600X175-10N; Mouser Part Number 250-A3909GLNTR-T
IC3, IC4: LTV-247; LTV247; Mouser Part Number 859-LTV-247
J1: USB_C_Receptacle_USB2.0; USB_C_Receptacle_HRO_TYPE-C-31-M-12
J2: CAM; JST-ZH-2_PIN
J3: Servo; PinSocket_1x03_P2.54mm_Vertical
J4: Hall-M1; PinHeader_1x03_P1.27mm_Vertical
J5: Hall-M2; PinHeader_1x03_P1.27mm_Vertical
J6: Hall-M0; PinHeader_1x03_P1.27mm_Vertical
J7: Hall-M3; PinHeader_1x03_P1.27mm_Vertical
M0, M1, M2, M3: Motor_DC_ALT; JST_EH_B2B-EH-A_1x02_P2.50mm_Vertical
Q1: SQ2348ES-T1_BE3; SOT-23-3
R1: R_LED; R_0603_1608Metric_Pad0.98x0.95mm_HandSolder
R2, R3: 5.1K; R_0603_1608Metric_Pad0.98x0.95mm_HandSolder
R4, R5, R6, R11, R12, R13, R14: 10K; R_0603_1608Metric_Pad0.98x0.95mm_HandSolder
R7, R9: 1K; R_0603_1608Metric_Pad0.98x0.95mm_HandSolder
R8: 100K; R_0603_1608Metric_Pad0.98x0.95mm_HandSolder
R10: 2K; R_0603_1608Metric_Pad0.98x0.95mm_HandSolder
R15: R_PWM; R_0603_1608Metric_Pad0.98x0.95mm_HandSolder
R16: R_OPTO; R_0603_1608Metric_Pad0.98x0.95mm_HandSolder
RV1: R_Potentiometer_Small; PinHeader_1x03_P2.00mm_Vertical
R_S0, R_S1, R_S2, R_S3: 0.01; R_1206_3216Metric
R_bat1: 90k; R_0805_2012Metric_Pad1.20x1.40mm_HandSolder
R_bat2: 50k; R_0805_2012Metric_Pad1.20x1.40mm_HandSolder
SW1: RST; SW_Push_6x6mm_H9.5mm
SW2: BOOT; SW_Push_6x6mm_H9.5mm
SW4: LSS12-P-V-B
U1: ESP32-S3-WROOM-1-N8
U2, U7: AZ1117IH-3.3TRG1; SOT-223-3_TabPin2
U4, U5: XS3A2467PWJ _TSSOP-16_4.4x5mm_P0.65mm
U6: INA4181A3IPWR; SOP65P640X120-20N
U8: LSM6DSM (LSM6DSMTR); LSM6DSM
U9: LM358_DFN; SOIC-8-1EP_3.9x4.9mm_P1.27mm_EP2.514x3.2mm

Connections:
/BUZZER_PIN: BZ1.1 (-), U1.38 (IO2)
/EN: C4.2, R4.1, SW1.2, U1.3 (EN)
/FWR_0: IC3.1 (A_1), U1.22 (IO14)
/FWR_1: IC3.5 (A_3), U1.30 (IO37)
/FWR_2: IC4.1 (A_1), U1.32 (IO39)
/FWR_3: IC4.7 (A_4), U1.34 (IO41)
/Hall_effect_0: J6.3, U1.4 (IO4)
/Hall_effect_1: J4.3, U1.5 (IO5)
/Hall_effect_2: J5.3, U1.6 (IO6)
/Hall_effect_3: J7.3, U1.7 (IO7)
/IO0: SW2.2, U1.27 (IO0)
/M0_DIR: U1.18 (IO10), U4.4 (1S)
/M0_sense: U1.8 (IO15), U6.2 (OUT1)
/M1_A: IC1.4 (IN3), U4.11 (3Y0), U4.13 (4Y1)
/M1_B: IC1.5 (IN4), U4.9 (3Y1), U4.15 (4Y0)
/M1_DIR: U1.19 (IO11), U4.12 (2S)
/M1_sense: U1.9 (IO16), U6.8 (OUT2)
/M2_A: IC2.1 (IN1), U5.3 (1Y0), U5.5 (2Y1)
/M2_B: IC2.2 (IN2), U5.1 (1Y1), U5.7 (2Y0)
/M2_DIR: U1.20 (IO12), U5.4 (1S)
/M2_sense: U1.10 (IO17), U6.13 (OUT3)
/M3_A: IC2.4 (IN3), U5.11 (3Y0), U5.13 (4Y1)
/M3_B: IC2.5 (IN4), U5.9 (3Y1), U5.15 (4Y0)
/M3_DIR: U1.21 (IO13), U5.12 (2S)
/M3_sense: U1.11 (IO18), U6.19 (OUT4)
/OPTO_3V3: IC3.10 (C_4), IC3.12 (C_3), IC3.14 (C_2), IC3.16 (C_1), IC4.10 (C_4), IC4.12 (C_3), IC4.14 (C_2), IC4.16 (C_1), R16.1
/OPTO_FWR_1: IC3.11 (E_3), U4.10 (3Z)
/OPTO_FWR_2: IC4.15 (E_1), U5.2 (1Z)
/OPTO_FWR_3: IC4.11 (E_3), U5.10 (3Z)
/OPTO_GND: IC3.2 (K_1), IC3.4 (K_2), IC3.6 (K_3), IC3.8 (K_4), IC4.2 (K_1), IC4.4 (K_2), IC4.6 (K_3), IC4.8 (K_4), R15.2
/OPTO_REV_0: IC3.13 (E_2), U4.6 (2Z)
/OPTO_REV_1: IC3.9 (E_4), U4.14 (4Z)
/OPTO_REV_2: IC4.13 (E_2), U5.6 (2Z)
/OPTO_REV_3: IC4.9 (E_4), U5.14 (4Z)
/REV_0: IC3.3 (A_2), U1.29 (IO36)
/REV_1: IC3.7 (A_4), U1.31 (IO38)
/REV_2: IC4.3 (A_2), U1.33 (IO40)
/REV_3: IC4.5 (A_3), U1.35 (IO42)
/SCL: R13.2, U1.17 (IO9), U8.13 (SCL)
/SDA: R12.2, U1.12 (IO8), U8.14 (SDA)
/Servo: J3.3, U1.39 (IO1)
/TAIL_LED: D2.2 (A), U1.28 (IO35)
/USB_D+: J1.A6 (D+), J1.B6 (D+), U1.14 (IO20)
/USB_D-: J1.A7 (D-), J1.B7 (D-), U1.13 (IO19)
/bat_level: R_bat1.2, R_bat2.1, U1.23 (IO21)
/in+0: M0.2 (-), R_S0.1, U6.4 (IN+1)
/in+1: M1.2 (-), R_S1.1, U6.6 (IN+2)
/in+2: M2.2 (-), R_S2.1, U6.15 (IN+3)
/in+3: M3.2 (-), R_S3.1, U6.17 (IN+4)
/in-0: C9.1, IC1.9 (OUT2), R_S0.2, U6.3 (IN-1)
/in-1: C11.1, IC1.6 (OUT4), R_S1.2, U6.7 (IN-2)
/in-2: C17.1, IC2.9 (OUT2), R_S2.2, U6.14 (IN-3)
/in-3: C18.1, IC2.6 (OUT4), R_S3.2, U6.18 (IN-4)
unnamed: ADR0.3 (B), R14.1
unnamed: ADR0.2 (C), U8.1 (SDO/SA0)
unnamed: BT1.2 (-), Q1.3 (D)
unnamed: D1.1 (K), R1.2
unnamed: D2.1 (K), R7.2
unnamed 59: C2.2, U2.3 (VI); also elsewhere on the board
unnamed: D5.2 (A), R9.1, SW4.2 (COM)
unnamed: D5.1 (K), R10.2
unnamed 62: J1.A4 (VBUS), J1.A9 (VBUS), J1.B4 (VBUS), J1.B9 (VBUS); also elsewhere on the board
unnamed: C9.2, IC1.10 (OUT1), M0.1 (+)
unnamed: C11.2, IC1.7 (OUT3), M1.1 (+)
unnamed: C17.2, IC2.10 (OUT1), M2.1 (+)
unnamed: C18.2, IC2.7 (OUT3), M3.1 (+)
unnamed: J1.A5 (CC1), R2.1
unnamed: J1.B5 (CC2), R3.1
unnamed: Q1.1 (G), R8.1, R9.2
unnamed: R11.1, SW4.3 (B)
unnamed: U6.1 (REF1), U6.9 (REF2), U6.12 (REF3), U6.20 (REF4), U9.1, U9.2 (-)
unnamed: R5.1, R6.1, RV1.2, U9.3 (+)
VCC: BT1.1 (+), C12.1, C14.1, C15.1, C16.1, C20.2, C22.2, D7.1 (K), IC1.3 (VBB), IC2.3 (VBB), R_bat1.1, SW4.1 (A); also elsewhere on the board

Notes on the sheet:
Boot
1K?
I2C Pullup resistors
Buzzer
Switch between forward/reverse with DPDT analog switch FWR: PWM, REV: LOW and FWR: LOW, REV: PWM
Tail LED
3V step down (from USB 5V)
500mA (h) fuse: 0ZCJ0050AF2E
Shared current limit resistors
"MODE 1": HOST<->IMU through SPI/I2C I2C Enabled: CS = 1 * THIS IS USED * SPI Enabled: CS = 0
AZ1117D-5.0TRE1
Buttons: TS04-66-50-BK-100-SMT
USB port
IMU
7.2-8.4V
Capacitors: EEV476M035S9GAA
Motor control
Servo connection
Battery measurement 8.4V -> 3.0V after divider
ESP reset
Current measurement
8.8V (5%)
ADD FERRIC CORE 0603
Camera connector (power)
PWR LED
3.6V (6%)
Battery and MOSFET with switch
3V step down
Optocoupler between ESP and logic input
5V step down
Voltage clamping with zener diodes
Hall effect sensors for the wheels: DRV5056A2QLPGM
GPIO35 has weak pull up on reset, moved FWR_0 away

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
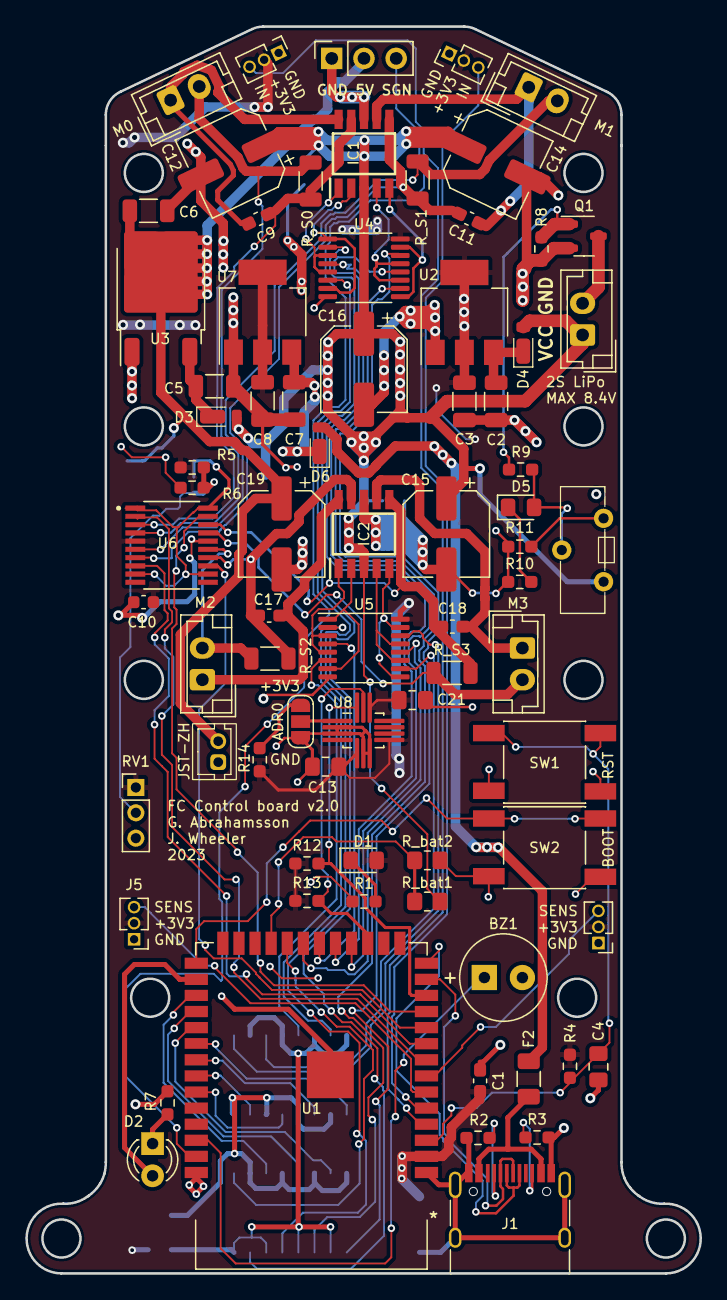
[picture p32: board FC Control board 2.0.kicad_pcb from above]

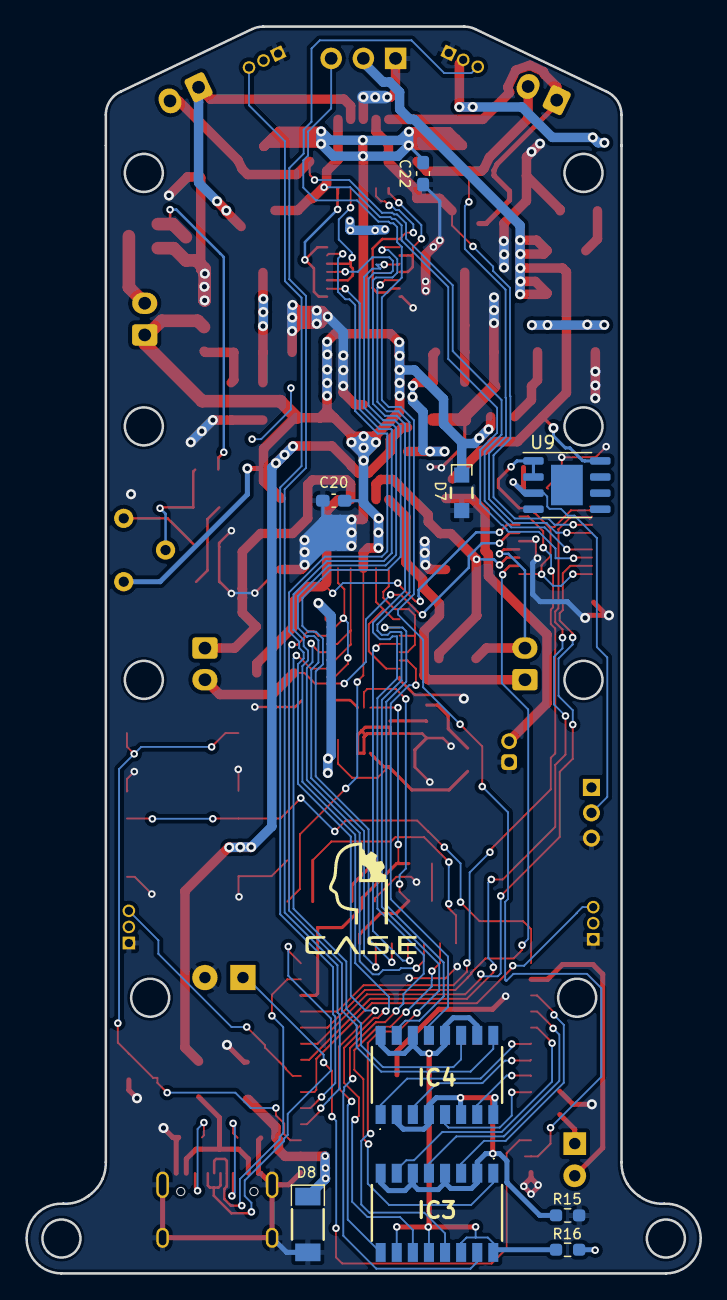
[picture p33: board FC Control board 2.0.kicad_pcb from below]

Board: 2 copper layers, 53.2 x 98.4 mm, 85 parts (9 on the bottom side), 82 nets.

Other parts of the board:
C5, C6: 10uF; C_1206_3216Metric
D3, D4, D6: CUHS20S30,H3F
F2: PPTC 500mA; Fuse_1206_3216Metric
U3: AZ1117D-5.0TRE1; TO-252-2

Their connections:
/USB_VBUS: D6.2 (A), F2.2
unnamed 59: D4.1 (K); also elsewhere on the board
unnamed 62: F2.1; also elsewhere on the board
VCC: D3.2 (A), D4.2 (A); also elsewhere on the board

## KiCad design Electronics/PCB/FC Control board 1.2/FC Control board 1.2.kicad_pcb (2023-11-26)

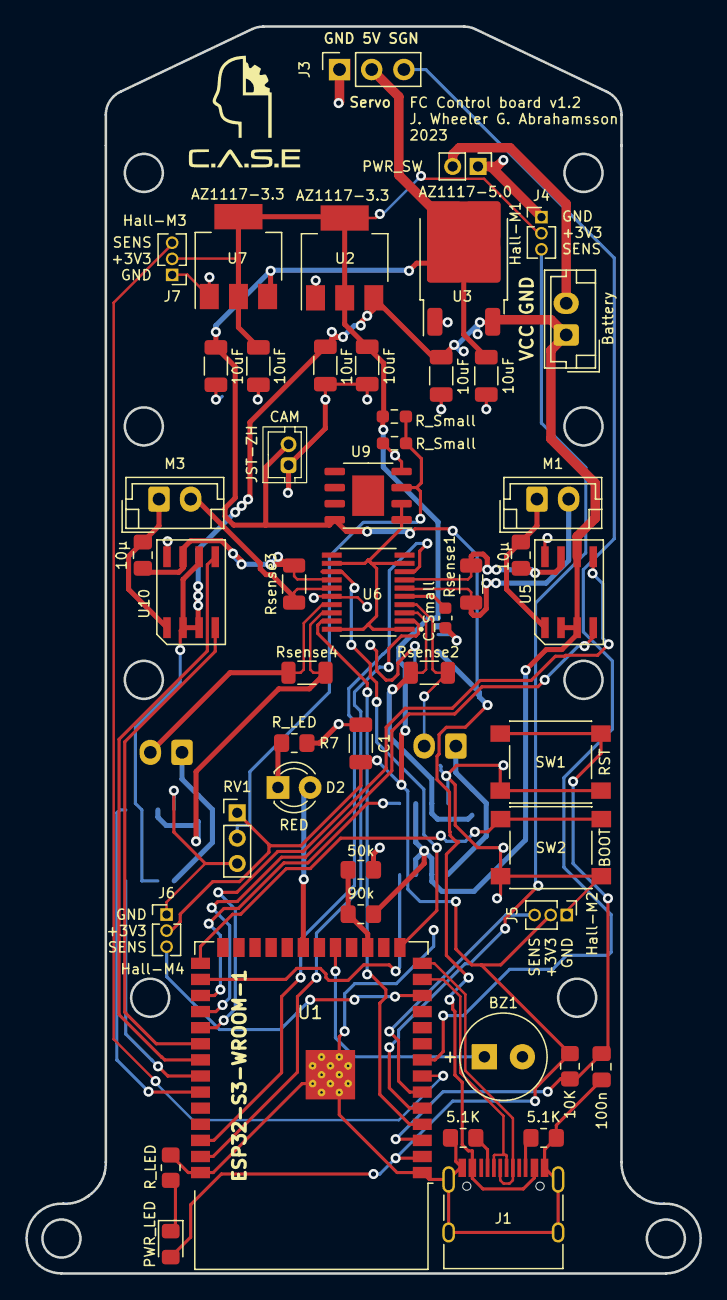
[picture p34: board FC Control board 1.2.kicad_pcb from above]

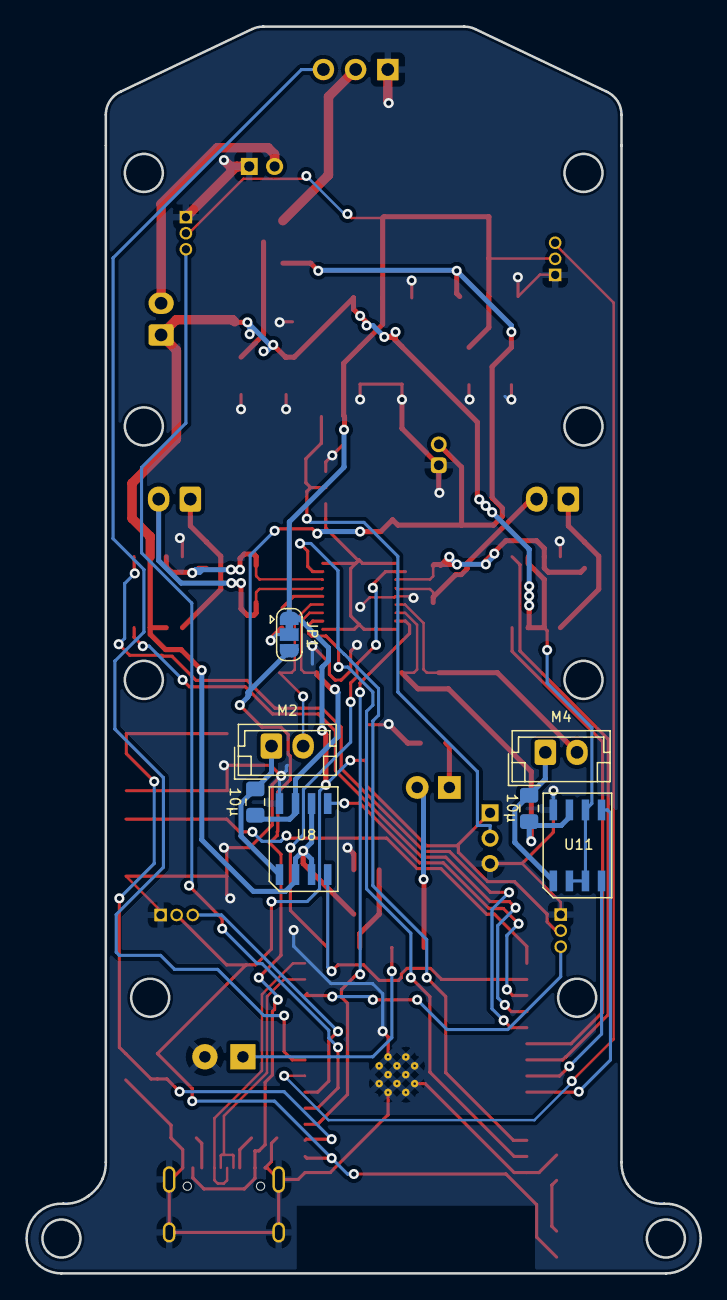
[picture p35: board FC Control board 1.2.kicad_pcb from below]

Board: 2 copper layers, 53.2 x 98.4 mm, 56 parts (7 on the bottom side), 49 nets.

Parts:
BT1: Battery; JST_EH_B2B-EH-A_1x02_P2.50mm_Vertical
BZ1: AC-703R-P4; MagneticBuzzer_Kobitone_254-EMB73-RO
C1: C; C_1206_3216Metric
C2, C3, C5, C6, C7, C8: 10uF; C_1206_3216Metric
C4: 100n; C_0805_2012Metric_Pad1.18x1.45mm_HandSolder
C10: C_Small; C_0603_1608Metric
C11, C12, C13, C14: 10µ; C_0805_2012Metric_Pad1.18x1.45mm_HandSolder
D1: PWR_LED; LED_0805_2012Metric_Pad1.15x1.40mm_HandSolder
D2: RED; LED_D3.0mm
J1: USB_C_Receptacle_USB2.0; USB_C_Receptacle_HRO_TYPE-C-31-M-12
J2: CAM; JST-ZH-2_PIN
J3: Servo; PinSocket_1x03_P2.54mm_Vertical
J4: Hall-M1; PinHeader_1x03_P1.27mm_Vertical
J5: Hall-M2; PinHeader_1x03_P1.27mm_Vertical
J6: Hall-M4; PinHeader_1x03_P1.27mm_Vertical
J7: Hall-M3; PinHeader_1x03_P1.27mm_Vertical
JP1: SolderJumper_3_Bridged12; SolderJumper-3_P1.3mm_Bridged12_RoundedPad1.0x1.5mm
M1, M2, M3, M4: Motor_DC_ALT; JST_EH_B2B-EH-A_1x02_P2.50mm_Vertical
R1, R7: R_LED; R_0805_2012Metric_Pad1.20x1.40mm_HandSolder
R2, R3: 5.1K; R_0805_2012Metric_Pad1.20x1.40mm_HandSolder
R4: 10K; R_0805_2012Metric_Pad1.20x1.40mm_HandSolder
R5, R6: R_Small; R_0603_1608Metric_Pad0.98x0.95mm_HandSolder
RV1: R_Potentiometer_Small; PinHeader_1x03_P2.00mm_Vertical
R_bat1: 90k; R_0805_2012Metric_Pad1.20x1.40mm_HandSolder
R_bat2: 50k; R_0805_2012Metric_Pad1.20x1.40mm_HandSolder
Rsense1, Rsense2, Rsense3, Rsense4: R_Small; R_1206_3216Metric
SW1: RST; SW_Push_1P1T_NO_6x6mm_H9.5mm
SW2: BOOT; SW_Push_1P1T_NO_6x6mm_H9.5mm
SW3: PWR_SW; PinHeader_1x02_P2.00mm_Vertical
U1: ESP32-S3-WROOM-1-N8; ESP32-S3-WROOM-1
U2, U7: AZ1117-3.3; SOT-223-3_TabPin2
U3: AZ1117-5.0; TO-252-2
U5, U8, U10, U11: ZXBM5210
U6: INA4181A3IPWR; SOP65P640X120-20N
U9: LM358_DFN; SOIC-8-1EP_3.9x4.9mm_P1.27mm_EP2.514x3.2mm

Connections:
+3V3: C1.2, C3.2, C8.2, D1.2 (A), J4.2, J5.2, J6.2, J7.2, JP1.1 (A), R4.2, R5.2, RV1.1, U1.2 (3V3), U2.2 (VO), U7.2 (VO)
+5V: C6.2, C7.2, J1.A4 (VBUS), J1.A9 (VBUS), J1.B4 (VBUS), J1.B9 (VBUS), J2.2, J3.2, JP1.3 (B), U3.2 (VO), U7.3 (VI), U9.8 (V+)
/ADC1_8: R_bat1.2, R_bat2.1, U1.17 (IO9)
/BUZZER_PIN: BZ1.1 (-), U1.19 (IO11)
/EN: C4.2, R4.1, SW1.2, U1.3 (EN)
/FWR_1: U1.28 (IO35), U8.4 (FWD)
/FWR_2: U1.30 (IO37), U5.4 (FWD)
/FWR_3: U1.32 (IO39), U10.4 (FWD)
/FWR_4: U1.34 (IO41), U11.4 (FWD)
/Hall_effect_1: J4.3, U1.5 (IO5)
/Hall_effect_2: J5.3, U1.6 (IO6)
/Hall_effect_3: J7.3, U1.7 (IO7)
/Hall_effect_4: J6.3, U1.12 (IO8)
/IO0: SW2.2, U1.27 (IO0)
/M1_sense: U1.39 (IO1), U6.2 (OUT1)
/M2_sense: U1.38 (IO2), U6.8 (OUT2)
/M3_sense: U1.15 (IO3), U6.13 (OUT3)
/M4_sense: U1.4 (IO4), U6.19 (OUT4)
/REV_1: U1.29 (IO36), U8.5 (REV)
/REV_2: U1.31 (IO38), U5.5 (REV)
/REV_3: U1.33 (IO40), U10.5 (REV)
/REV_4: U1.35 (IO42), U11.5 (REV)
/Servo: J3.3, U1.8 (IO15)
/TAIL_LED: D2.2 (A), U1.21 (IO13)
/USB_D+: J1.A6 (D+), J1.B6 (D+), U1.14 (IO20)
/USB_D-: J1.A7 (D-), J1.B7 (D-), U1.13 (IO19)
/in+1: M2.2 (-), Rsense2.1, U6.4 (IN+1)
/in+2: M1.2 (-), Rsense1.1, U6.6 (IN+2)
/in+3: M3.2 (-), Rsense3.1, U6.15 (IN+3)
/in+4: M4.2 (-), Rsense4.1, U6.17 (IN+4)
/in-1: C11.2, Rsense2.2, U6.3 (IN-1), U8.7 (OUT2)
/in-2: C12.2, Rsense1.2, U5.7 (OUT2), U6.7 (IN-2)
/in-3: C13.2, Rsense3.2, U6.14 (IN-3), U10.7 (OUT2)
/in-4: C14.2, Rsense4.2, U6.18 (IN-4), U11.7 (OUT2)
GNDREF: BZ1.2 (+), C1.1, C2.1, C3.1, C4.1, C5.1, C6.1, C7.1, C8.1, J1.A1 (GND), J1.A12 (GND), J1.B1 (GND), J1.B12 (GND), J1.S1 (SHIELD), J2.1, J3.1, J4.1, J5.1, J6.1, J7.1, R1.1, R2.2, R3.2, R6.2, R7.1, RV1.3, R_bat2.2, SW1.1, SW2.1, SW3.1 (A), U1.1 (GND), U1.40 (GND), U1.41 (GND), U2.1 (GND), U3.1 (GND), U5.8 (GND), U6.16 (GND), U7.1 (GND), U8.8 (GND), U9.4 (V-), U10.8 (GND), U11.8 (GND)
unnamed: BT1.2 (-), SW3.2 (B)
unnamed: D1.1 (K), R1.2
unnamed: D2.1 (K), R7.2
unnamed: J1.A5 (CC1), R2.1
unnamed: J1.B5 (CC2), R3.1
unnamed: C10.1, JP1.2 (C)
unnamed: C12.1, M1.1 (+), U5.1 (Out1)
unnamed: C11.1, M2.1 (+), U8.1 (Out1)
unnamed: C13.1, M3.1 (+), U10.1 (Out1)
unnamed: C14.1, M4.1 (+), U11.1 (Out1)
unnamed: U6.1 (REF1), U6.9 (REF2), U6.12 (REF3), U6.20 (REF4), U9.1, U9.2 (-)
unnamed: C10.2, U6.5 (VS)
unnamed: R5.1, R6.1, RV1.2, U9.3 (+)
VCC: BT1.1 (+), C2.2, C5.2, R_bat1.1, U2.3 (VI), U3.3 (VI), U5.2 (Vm), U5.3 (Vdd), U5.6 (Vref), U8.2 (Vm), U8.3 (Vdd), U8.6 (Vref), U10.2 (Vm), U10.3 (Vdd), U10.6 (Vref), U11.2 (Vm), U11.3 (Vdd), U11.6 (Vref)

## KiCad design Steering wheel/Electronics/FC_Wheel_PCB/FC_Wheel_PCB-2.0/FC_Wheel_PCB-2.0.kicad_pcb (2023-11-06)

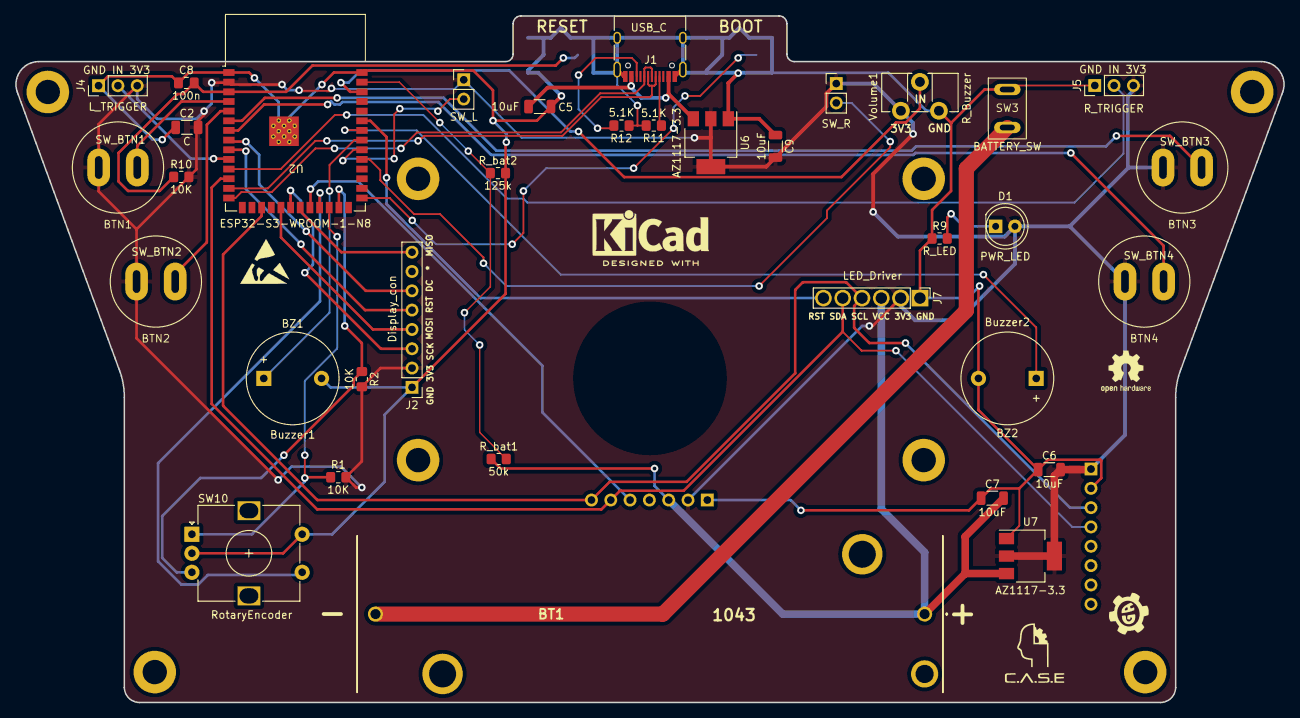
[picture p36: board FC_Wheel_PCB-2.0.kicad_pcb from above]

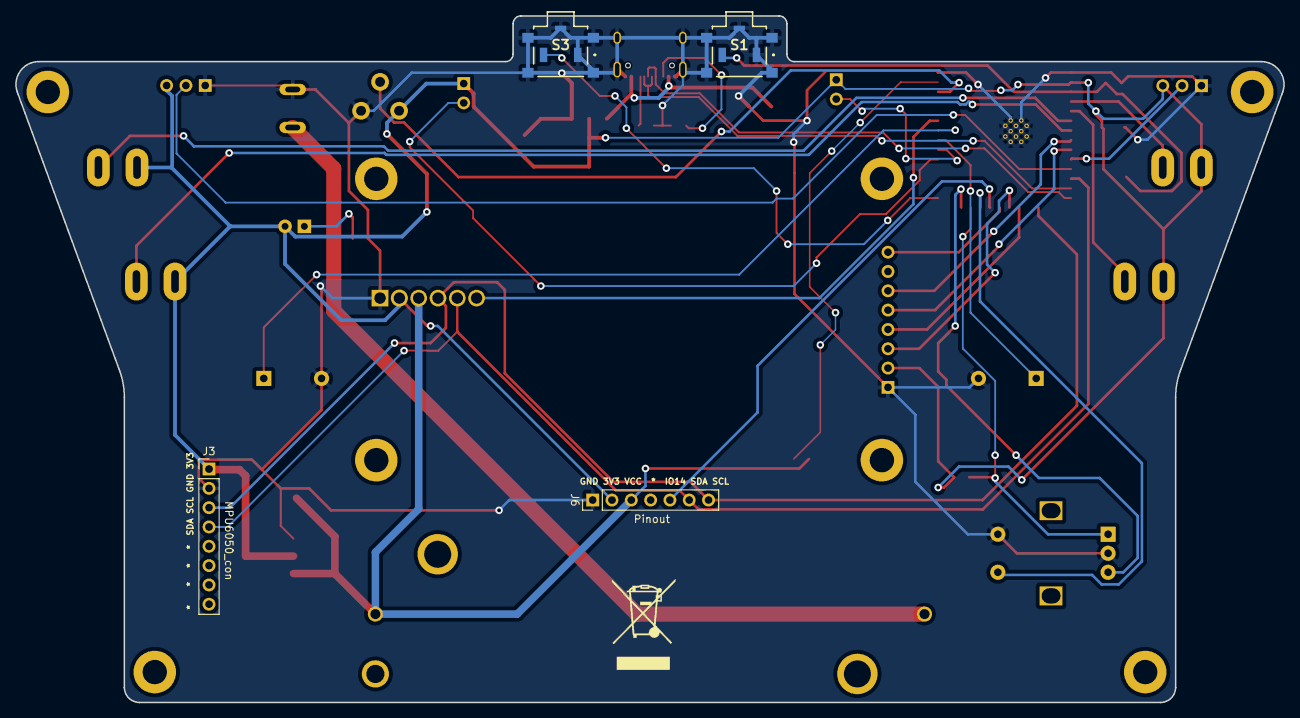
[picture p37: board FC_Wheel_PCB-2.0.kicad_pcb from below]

Board: 2 copper layers, 166.8 x 90.3 mm, 39 parts (4 on the bottom side), 36 nets.

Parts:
BT1: Battery; 1043_fromMouser
BTN1: SW_BTN1; SPST_PushButton_Cyl
BTN2: SW_BTN2; SPST_PushButton_Cyl
BTN3: SW_BTN3; SPST_PushButton_Cyl
BTN4: SW_BTN4; SPST_PushButton_Cyl
BZ1: Buzzer1; Buzzer_12x9.5RM7.6
BZ2: Buzzer2; Buzzer_12x9.5RM7.6
C2: C; C_1206_3216Metric
C5, C6, C7, C9: 10uF; C_1206_3216Metric
C8: 100n; C_0805_2012Metric_Pad1.18x1.45mm_HandSolder
D1: PWR_LED; LED_D5.0mm
J1: USB_C; USB_C_Receptacle_HRO_TYPE-C-31-M-12
J2: Display_con; PinHeader_1x08_P2.54mm_Vertical
J3: MPU6050_con; PinHeader_1x08_P2.54mm_Vertical
J4: L_TRIGGER; PinHeader_1x03_P2.54mm_Vertical
J5: R_TRIGGER; PinHeader_1x03_P2.54mm_Vertical
J6: Pinout; PinHeader_1x07_P2.54mm_Vertical
J7: LED_Driver; PinHeader_1x06_P2.54mm_Vertical
PADDLE1: SW_R; PinHeader_1x02_P2.54mm_Vertical
PADDLE2: SW_L; PinHeader_1x02_P2.54mm_Vertical
R1, R2, R10: 10K; R_0805_2012Metric_Pad1.20x1.40mm_HandSolder
R9: R_LED; R_0805_2012Metric_Pad1.20x1.40mm_HandSolder
R11, R12: 5.1K; R_0805_2012Metric_Pad1.20x1.40mm_HandSolder
R_bat1: 50k; R_0805_2012Metric_Pad1.20x1.40mm_HandSolder
R_bat2: 125k; R_0805_2012Metric_Pad1.20x1.40mm_HandSolder
S1, S3: TL3336AF160Q
SW3: BATTERY_SW; STST Switch 2MS6T1B3M2QES
SW10: RotaryEncoder; RotaryEncoder_Alps_EC12E-Switch_Vertical_H20mm
U2: ESP32-S3-WROOM-1-N8; ESP32-S3-WROOM-1_handsolder
U6, U7: AZ1117-3.3; SOT-223-3_TabPin2
Volume1: R_Buzzer; Potentiometer_ACP_CA9-H3,8_Horizontal

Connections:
+3V3: BTN1.1 (A), BTN2.1 (A), BTN3.1 (A), BTN4.1 (A), C2.2, C6.2, C9.2, D1.2 (A), J2.2, J3.1, J4.3, J5.3, J6.2, J7.2, PADDLE1.1 (A), PADDLE2.1 (A), R1.2, R2.2, R10.2, U2.2 (3V3), U6.2 (VO), U7.2 (VO), Volume1.1
+5V: C5.2, J1.A4 (VBUS), J1.A9 (VBUS), J1.B4 (VBUS), J1.B9 (VBUS), U6.3 (VI)
/BTN1: BTN1.2 (B), U2.4 (IO4)
/BTN2: BTN2.2 (B), U2.5 (IO5)
/BTN3: BTN3.2 (B), U2.6 (IO6)
/BTN4: BTN4.2 (B), U2.7 (IO7)
/BUZZER_PIN1: BZ1.1 (-), U2.33 (IO40)
/BUZZER_PIN2: BZ2.1 (-), U2.34 (IO41)
/DC: J2.6, U2.8 (IO15)
/EN: C8.2, R10.1, S1.2 (NO), U2.3 (EN)
/ENC_A: R1.1, SW10.A, U2.24 (IO47)
/ENC_B: R2.1, SW10.B, U2.25 (IO48)
/ENC_SW: SW10.S2, U2.23 (IO21)
/IO0: S3.2 (NO), U2.27 (IO0)
/IO14: J6.5, U2.22 (IO14)
/LED_RESET: J7.6, U2.35 (IO42)
/L_PADDLE: PADDLE2.2 (B), U2.32 (IO39)
/L_TRIGGER: J4.2, U2.10 (IO17)
/MISO: J2.8, U2.21 (IO13)
/MOSI: J2.4, U2.19 (IO11)
/RST: J2.5, U2.9 (IO16)
/R_PADDLE: PADDLE1.2 (B), U2.31 (IO38)
/R_TRIGGER: J5.2, U2.11 (IO18)
/SCK: J2.3, U2.20 (IO12)
/SCL: J3.3, J6.7, J7.4, U2.17 (IO9)
/SDA: J3.4, J6.6, J7.5, U2.12 (IO8)
/USB_D+: J1.A6 (D+), J1.B6 (D+), U2.14 (IO20)
/USB_D-: J1.A7 (D-), J1.B7 (D-), U2.13 (IO19)
/Volume_pot: U2.38 (IO2), Volume1.2
/bat_level: R_bat1.2, R_bat2.1, U2.39 (IO1)
Earth: BZ1.2 (+), BZ2.2 (+), C2.1, C5.1, C6.1, C7.1, C8.1, C9.1, J1.A1 (GND), J1.A12 (GND), J1.B1 (GND), J1.B12 (GND), J1.S1 (SHIELD), J2.1, J3.2, J4.1, J5.1, J6.1, J7.1, R9.1, R11.2, R12.2, R_bat2.2, S1.1 (COM), S1.MP1, S1.MP2, S1.MP3, S1.MP4, S1.MP5, S3.1 (COM), S3.MP1, S3.MP2, S3.MP3, S3.MP4, S3.MP5, SW3.1 (A), SW10.C, SW10.S1, U2.1 (GND), U2.40 (GND), U2.41 (GND), U6.1 (GND), U7.1 (GND), Volume1.3
unnamed: BT1.2 (-), SW3.2 (B)
unnamed: D1.1 (K), R9.2
unnamed: J1.A5 (CC1), R11.1
unnamed: J1.B5 (CC2), R12.1
VCC: BT1.1 (+), C7.2, J6.3, J7.3, R_bat1.1, U7.3 (VI)

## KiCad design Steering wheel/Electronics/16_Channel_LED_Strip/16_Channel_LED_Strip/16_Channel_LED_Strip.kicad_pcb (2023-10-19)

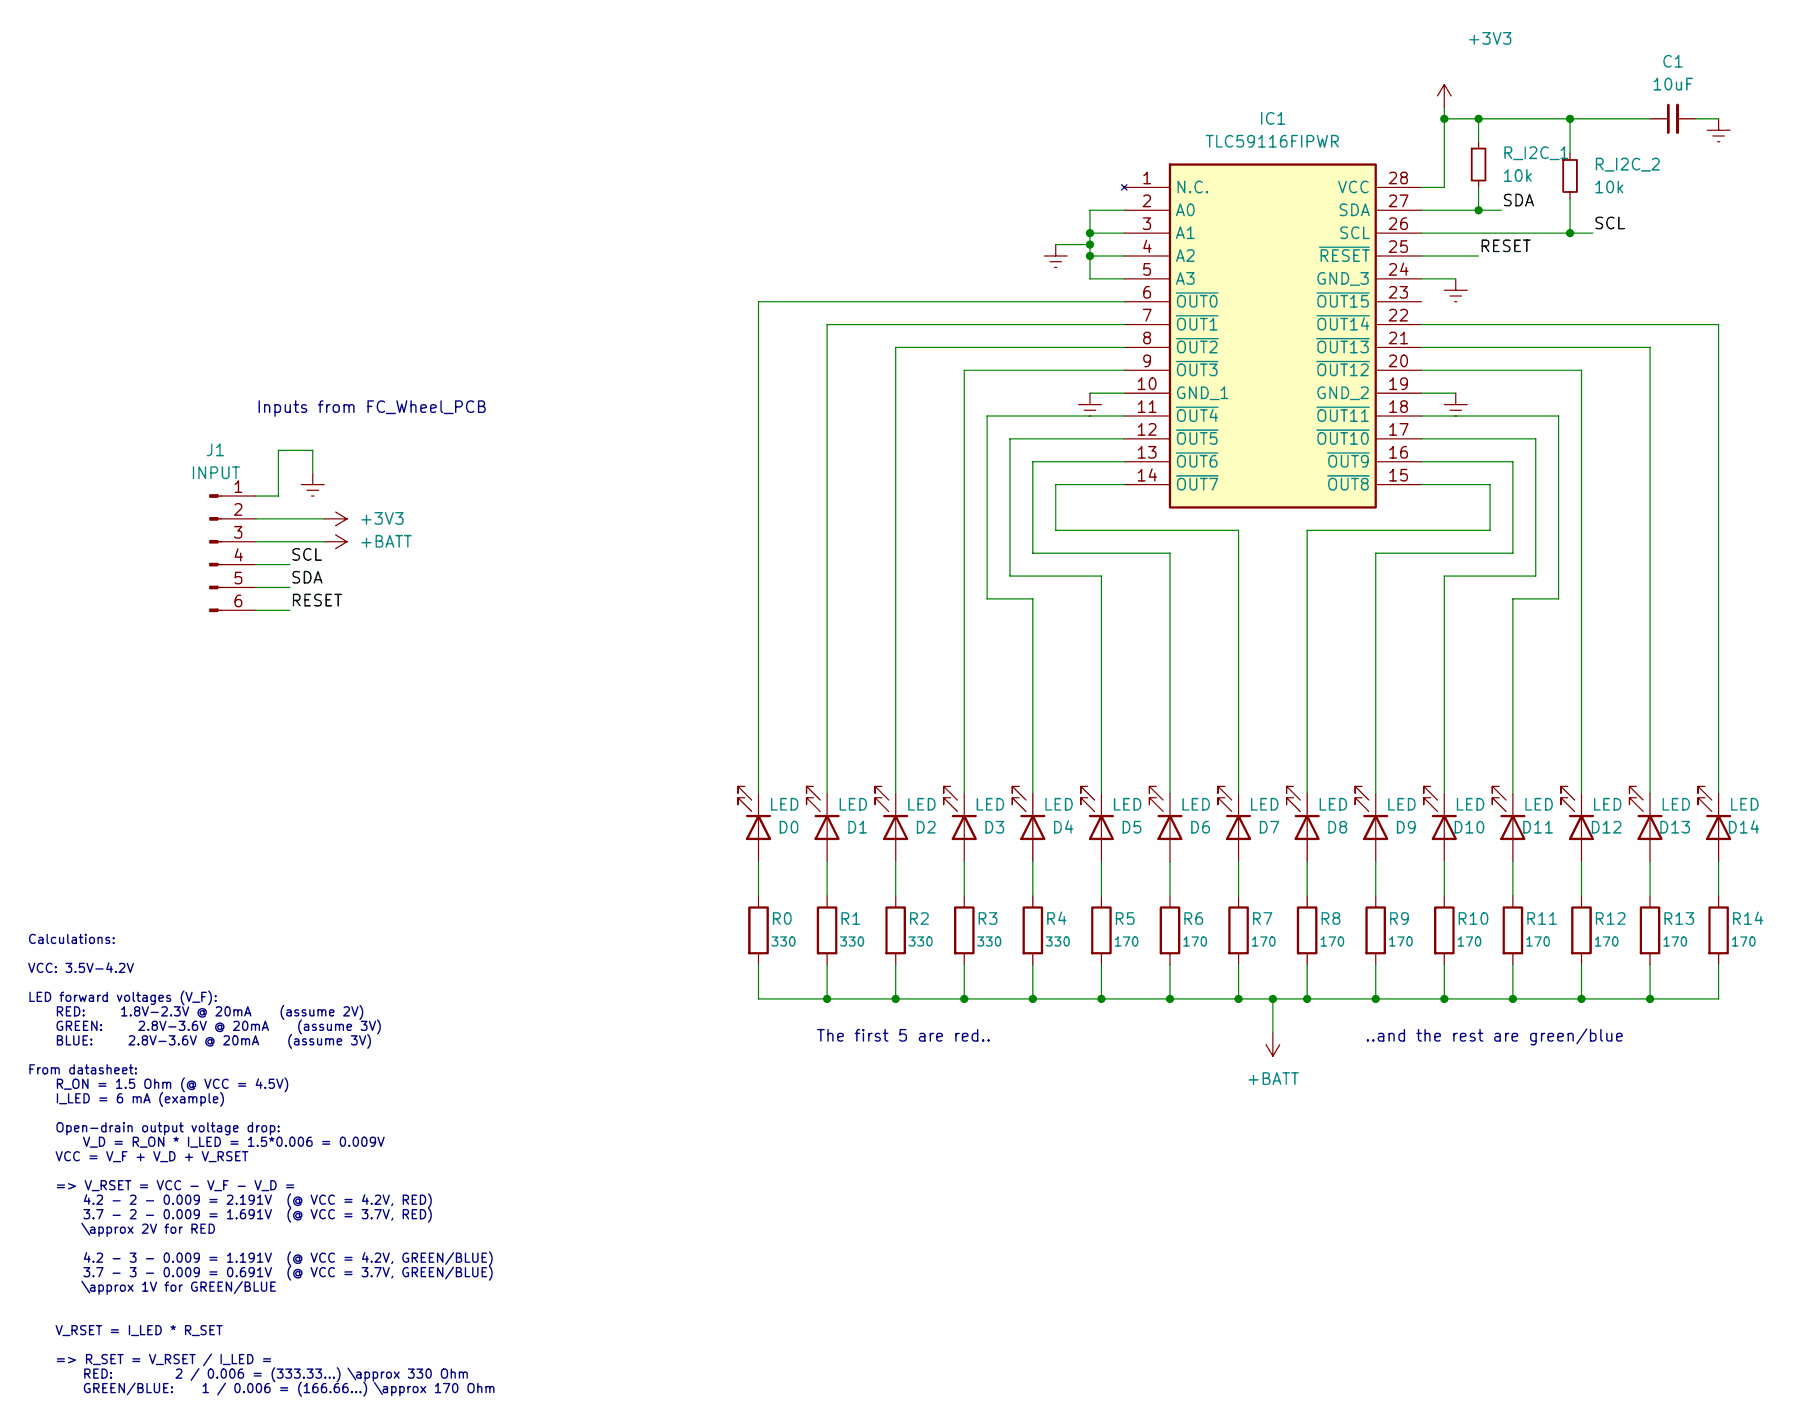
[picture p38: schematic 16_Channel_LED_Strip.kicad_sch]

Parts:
C1: 10uF; C_0805_2012Metric_Pad1.18x1.45mm_HandSolder
D0, D1, D2, D3, D4, D5, D6, D7, D8, D9, D10, D11, D12, D13, D14: LED; LED_D5.0mm
IC1: TLC59116FIPWR; SOP65P640X120-28N; Mouser Part Number 595-TLC59116FIPWR
J1: INPUT; PinHeader_1x06_P2.54mm_Vertical
R0, R1, R2, R3, R4: 330; R_0805_2012Metric_Pad1.20x1.40mm_HandSolder
R5, R6, R7, R8, R9, R10, R11, R12, R13, R14: 170; R_0805_2012Metric_Pad1.20x1.40mm_HandSolder
R_I2C_1, R_I2C_2: 10k; R_0805_2012Metric_Pad1.20x1.40mm_HandSolder

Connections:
+3V3: C1.1, IC1.28 (VCC), J1.2, R_I2C_1.1, R_I2C_2.1
+BATT: J1.3, R0.2, R1.2, R2.2, R3.2, R4.2, R5.2, R6.2, R7.2, R8.2, R9.2, R10.2, R11.2, R12.2, R13.2, R14.2
/RESET: IC1.25 (~RESET), J1.6
/SCL: IC1.26 (SCL), J1.4, R_I2C_2.2
/SDA: IC1.27 (SDA), J1.5, R_I2C_1.2
Earth: C1.2, IC1.2 (A0), IC1.3 (A1), IC1.4 (A2), IC1.5 (A3), IC1.10 (GND_1), IC1.19 (GND_2), IC1.24 (GND_3), J1.1
unnamed: D0.2 (A), R0.1
unnamed: D0.1 (K), IC1.6 (~OUT0)
unnamed: D1.2 (A), R1.1
unnamed: D1.1 (K), IC1.7 (~OUT1)
unnamed: D2.2 (A), R2.1
unnamed: D2.1 (K), IC1.8 (~OUT2)
unnamed: D3.2 (A), R3.1
unnamed: D3.1 (K), IC1.9 (~OUT3)
unnamed: D4.2 (A), R4.1
unnamed: D4.1 (K), IC1.11 (~OUT4)
unnamed: D5.2 (A), R5.1
unnamed: D5.1 (K), IC1.12 (~OUT5)
unnamed: D6.2 (A), R6.1
unnamed: D6.1 (K), IC1.13 (~OUT6)
unnamed: D7.2 (A), R7.1
unnamed: D7.1 (K), IC1.14 (~OUT7)
unnamed: D8.2 (A), R8.1
unnamed: D8.1 (K), IC1.15 (~OUT8)
unnamed: D9.2 (A), R9.1
unnamed: D9.1 (K), IC1.16 (~OUT9)
unnamed: D10.2 (A), R10.1
unnamed: D10.1 (K), IC1.17 (~OUT10)
unnamed: D11.2 (A), R11.1
unnamed: D11.1 (K), IC1.18 (~OUT11)
unnamed: D12.2 (A), R12.1
unnamed: D12.1 (K), IC1.20 (~OUT12)
unnamed: D13.2 (A), R13.1
unnamed: D13.1 (K), IC1.21 (~OUT13)
unnamed: D14.2 (A), R14.1
unnamed: D14.1 (K), IC1.22 (~OUT14)

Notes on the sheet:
The first 5 are red..
Inputs from FC_Wheel_PCB
..and the rest are green/blue
Calculations: VCC: 3.5V-4.2V LED forward voltages (V_F): RED: 1.8V-2.3V @ 20mA (assume 2V) GREEN: 2.8V-3.6V @ 20mA (assume 3V) BLUE: 2.8V-3.6V @ 20mA (assume 3V) From datasheet: R_ON = 1.5 Ohm (@ VCC = 4.5V) I_LED = 6 mA (example) Open-drain output voltage drop: V_D = R_ON * I_LED = 1.5*0.006 = 0.0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

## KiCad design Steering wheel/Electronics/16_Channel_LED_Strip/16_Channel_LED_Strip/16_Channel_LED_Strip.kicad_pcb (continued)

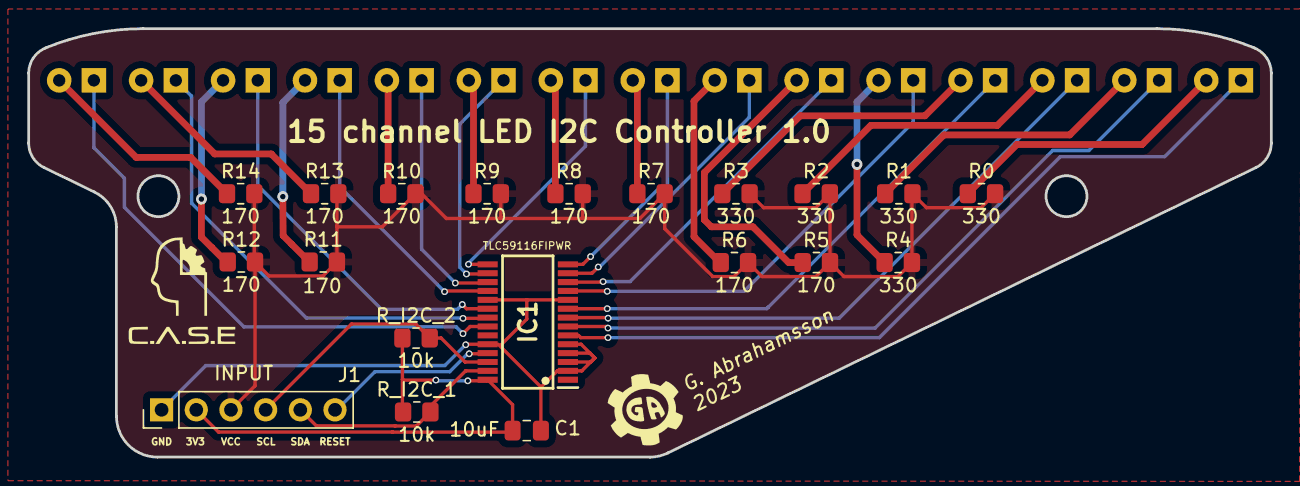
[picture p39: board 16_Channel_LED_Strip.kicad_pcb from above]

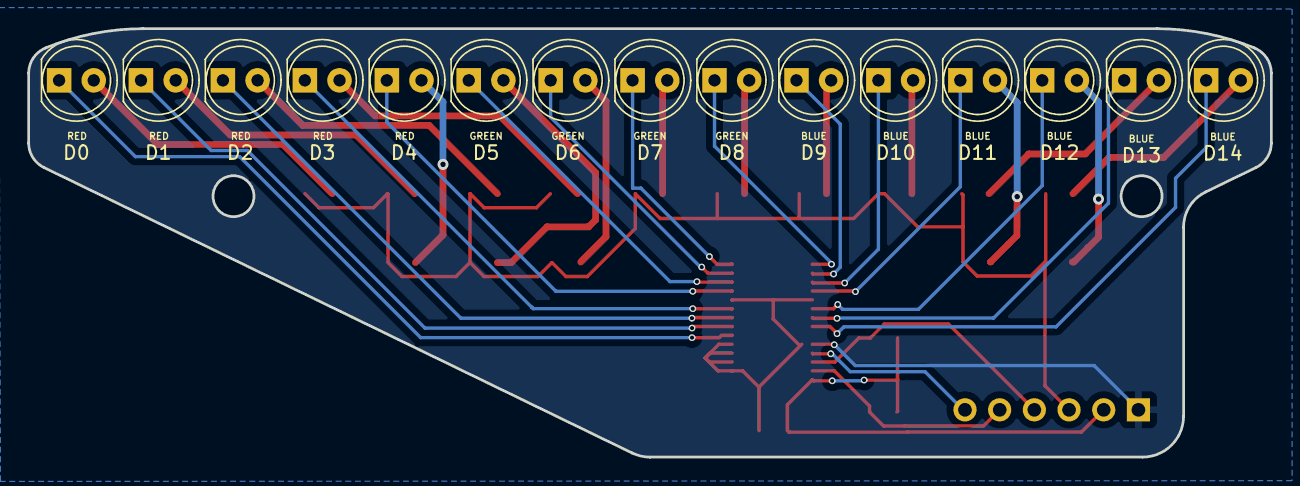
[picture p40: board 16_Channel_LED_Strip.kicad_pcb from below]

Board: 2 copper layers, 91.0 x 31.4 mm, 35 parts (15 on the bottom side), 36 nets.

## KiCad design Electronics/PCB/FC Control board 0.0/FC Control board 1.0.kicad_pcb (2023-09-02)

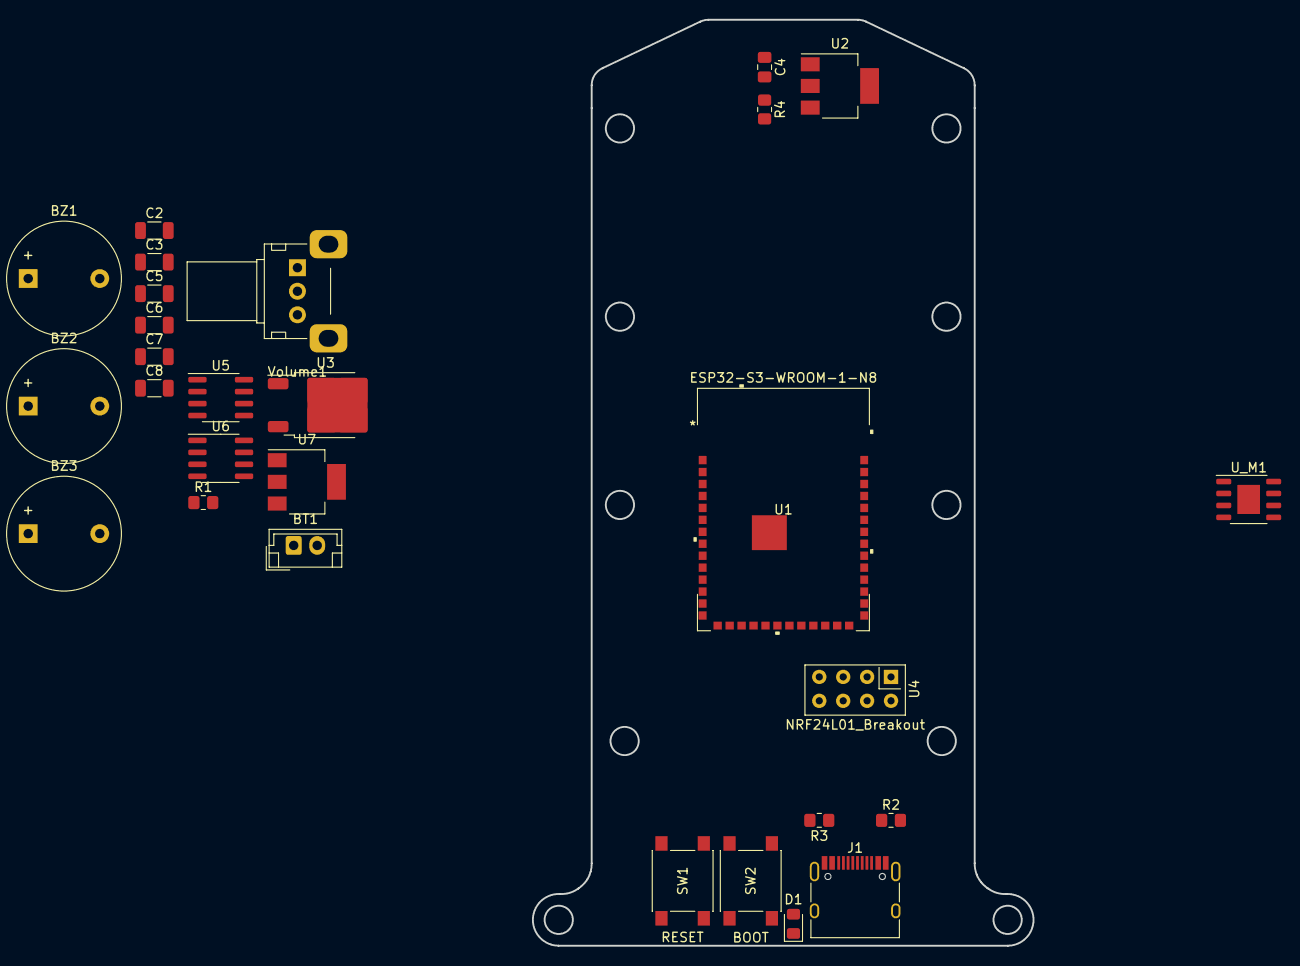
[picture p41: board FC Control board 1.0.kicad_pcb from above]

Board: 2 copper layers, 53.2 x 98.4 mm, 28 parts (0 on the bottom side), 21 nets, no tracks yet.

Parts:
BT1: Battery; JST_EH_B2B-EH-A_1x02_P2.50mm_Vertical
BZ1: Buzzer1; Buzzer_12x9.5RM7.6
BZ2: Buzzer2; Buzzer_12x9.5RM7.6
BZ3: Buzzer3; Buzzer_12x9.5RM7.6
C2, C3, C5, C6, C7, C8: 10uF; C_1206_3216Metric
C4: 100n; C_0805_2012Metric_Pad1.18x1.45mm_HandSolder
D1: PWR_LED; LED_0805_2012Metric_Pad1.15x1.40mm_HandSolder
J1: USB_C_Receptacle_USB2.0; USB_C_Receptacle_HRO_TYPE-C-31-M-12
R1: R_LED; R_0805_2012Metric_Pad1.20x1.40mm_HandSolder
R2, R3: 5.1K; R_0805_2012Metric_Pad1.20x1.40mm_HandSolder
R4: 10K; R_0805_2012Metric_Pad1.20x1.40mm_HandSolder
SW1: RESET; SW_Push_1P1T_NO_6x6mm_H9.5mm
SW2: BOOT; SW_Push_1P1T_NO_6x6mm_H9.5mm
U1: ESP32-S3-WROOM-1-N8
U2, U7: AZ1117-3.3; SOT-223-3_TabPin2
U3: AZ1117-5.0; TO-252-2
U4: NRF24L01_Breakout; nRF24L01_Breakout
U5: LM358DRG3 2_4; SOIC-8_3.9x4.9mm_P1.27mm
U6: LM358DRG3 1_3; SOIC-8_3.9x4.9mm_P1.27mm
U_M1: TB67H451AFNG,EL; HSOP-8-1EP_3.9x4.9mm_P1.27mm_EP2.41x3.1mm
Volume1: R_Buzzer; Potentiometer_Alps_RK09K_Single_Horizontal

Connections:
+3V3: C3.2, C8.2, D1.2 (A), R4.2, U1.2 (3V3), U2.2 (VO), U4.2 (VCC), U7.2 (VO), Volume1.1, Volume1.2
+5V: C6.2, C7.2, J1.A4 (VBUS), J1.A9 (VBUS), J1.B4 (VBUS), J1.B9 (VBUS), U3.2 (VO), U7.3 (VI)
/CE: U1.6 (IO6), U4.3 (CE)
/CSN: U1.5 (IO5), U4.4 (~CSN)
/EN: C4.2, R4.1, SW1.2, U1.3 (EN)
/IO0: SW2.2, U1.27 (IO0)
/M1_ref_3V: U1.28 (IO35), U6.5 (+)
/M2_ref_3V: U1.29 (IO36), U5.3 (+)
/M3_ref_3V: U1.30 (IO37), U5.5 (+)
/M4_ref_3V: U1.31 (IO38), U6.3 (+)
/MISO: U1.21 (IO13), U4.7 (MISO)
/MOSI: U1.19 (IO11), U4.6 (MOSI)
/SCK: U1.20 (IO12), U4.5 (SCK)
/USB_D+: J1.A6 (D+), J1.B6 (D+), U1.14 (IO20)
/USB_D-: J1.A7 (D-), J1.B7 (D-), U1.13 (IO19)
/Volume_pot: U1.7 (IO7), Volume1.3
GNDREF: BZ1.2 (+), BZ2.2 (+), BZ3.2 (+), C2.1, C3.1, C4.1, C5.1, C6.1, C7.1, C8.1, J1.A1 (GND), J1.A12 (GND), J1.B1 (GND), J1.B12 (GND), J1.S1 (SHIELD), R1.1, R2.2, R3.2, SW1.1, SW2.1, U1.1 (GND), U1.40 (GND), U1.41 (GND), U2.1 (GND), U3.1 (GND), U4.1 (GND), U5.4 (V-), U6.4 (V-), U7.1 (GND), U_M1.1 (GND)
unnamed: D1.1 (K), R1.2
unnamed: J1.A5 (CC1), R2.1
unnamed: J1.B5 (CC2), R3.1
VCC: BT1.1 (+), C2.2, C5.2, U2.3 (VI), U3.3 (VI), U5.8 (V+), U6.8 (V+), U_M1.5 (VM)

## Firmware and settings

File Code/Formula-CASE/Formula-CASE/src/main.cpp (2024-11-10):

#include <Arduino.h>
#include "esp_now.h"
#include "WiFi.h"
#include <ESP32Servo.h>

#include <Wire.h>
#include <deque>
#include <numeric>

//#include "Motor_controller.h"
#include "LSM6D_IMU.h"

LSM6D_IMU imu_LSM6D;

// Global control variable for testing
#define MOTORS_ALLOWED false

// Wheel 2.0 MAC: 34:85:18:5C:86:A0
uint8_t wheel_address[] = {0x34, 0x85, 0x18, 0x5C, 0x86, 0xA0};

// Car MAC: 0x34, 0x85, 0x18, 0x89, 0xE0, 0xA8
uint8_t car_address[] = {0x34, 0x85, 0x18, 0x89, 0xE0, 0xA8};

typedef struct wheel_to_car_msg {
    uint8_t throttle;
    uint8_t brake;
    float angle;
    int8_t gear;
} wheel_to_car_msg;

typedef struct car_to_wheel_msg {
    float w_ICE;
    float phi; // rad
    float hall;
} car_to_wheel_msg;

// ADC pins
#define HALL_EFF_0_PIN 4  // 0
#define HALL_EFF_1_PIN 5
#define HALL_EFF_2_PIN 6
#define HALL_EFF_3_PIN 7

// Buzzer
#define BUZZER_PIN 2

// Battery measurement
#define BAT_SENSE_PIN 21

// Motor direction pins
#define M0_DIR_PIN 10
#define M1_DIR_PIN 11
#define M2_DIR_PIN 12
#define M3_DIR_PIN 13

// Servo pins
#define SERVO_PIN 1

#define SERVO_DEFLECTION 50 // deg

#define M0_FWR_PIN 14 // 0
#define M0_REV_PIN 36 // 0
#define M1_FWR_PIN 37
#define M1_REV_PIN 38
#define M2_FWR_PIN 39
#define M2_REV_PIN 40
#define M3_FWR_PIN 41
#define M3_REV_PIN 42

// Assigned PWM channels
#define SERVO_CHL 0
#define M0_ASS_PWM_CHL 5
#define M1_ASS_PWM_CHL 2
#define M2_ASS_PWM_CHL 3
#define M3_ASS_PWM_CHL 4
#define BUZZER_CHNL 7

// Motor sense pins ADC
#define M0_SENSE_PIN 15 // 0
#define M1_SENSE_PIN 16
#define M2_SENSE_PIN 17
#define M3_SENSE_PIN 18

#define MOTOR_PWM_BIT_RES 8
#define MOTOR_PWM_FREQ 25000

// Tasks
#define MOTOR_TASK_FREQ 50 // Hz
#define MOTOR_TASK_CORE 1

#define PERIPH_TASK_FREQ 50 // Hz
#define PERIPH_TASK_CORE 1

#define SPEED_TASK_FREQ 100 // Hz
#define SPEED_TASK_CORE 1

#define RAD_PER_S_TO_RPM 9.54957
#define RPM_TO_RAD_PER_S 0.10471

// General
#define POWER_SCALING 0.5

// Powertrain simulation        R   N   1    2    3    4     5     6     7    8
const float GEAR_RATIOS[10] = {1.0, 0, 1.0, 0.85, 0.65, 0.55, 0.4, 0.3, 0.25, 0.2};

int8_t current_gear = 0;

const uint8_t num_old_w_samples = 5;

struct motor_measurement {
  float w_m;      // Wheel speed, RPM
  std::deque<float> w_stored;
  float phi;      // Wheel angle, rad
  float phi_last; // Old angle, rad
  int16_t hall_val; // Raw measurement from analogRead()
  int16_t max;
  int16_t min;
  int16_t mid;
  uint8_t pin;

  motor_measurement() : w_stored(num_old_w_samples, 0.0) {}
};
// float w_last;   // Old speed, RPM

motor_measurement m_meas[4];

car_to_wheel_msg outgoing_message;

wheel_to_car_msg incoming_message;

esp_now_peer_info_t peerInfo;
String success;
// Callback when data is sent
void OnDataSent(const uint8_t *mac_addr, esp_now_send_status_t status) {
  // Serial.print("\r\nLast Packet Send Status:\t");
  // Serial.println(status == ESP_NOW_SEND_SUCCESS ? "Delivery Success" : "Delivery Fail");
  if (status == 0){
    success = "Delivery Success :)";
  }
  else{
    success = "Delivery Fail :(";
  }
}

uint8_t wheel_throttle;
uint8_t wheel_brake;
float wheel_angle;

Servo servo;

// Callback when data is received
void OnDataRecv(const uint8_t * mac, const uint8_t *incomingData, int len) {
  memcpy(&incoming_message, incomingData, sizeof(incoming_message));
  // Serial.print("Bytes received: ");
  // Serial.println(len);
}
  
// Play a certain frequency via buzzer
void buzz_hz(uint16_t freq){
  ledcWriteTone(BUZZER_CHNL, freq);
}

void init_esp_now(){
  // Set device as a Wi-Fi Station
  WiFi.mode(WIFI_STA);

  // Init ESP-NOW
  if (esp_now_init() != ESP_OK) {
    Serial.println("Error initializing ESP-NOW");
    return;
  }

  // Once ESPNow is successfully Init, we will register for Send CB to
  // get the status of Trasnmitted packet
  esp_now_register_send_cb(OnDataSent);
  
  // Register peer
  memcpy(peerInfo.peer_addr, wheel_address, 6);
  peerInfo.channel = 0;  
  peerInfo.encrypt = false;
  
  // Add peer        
  if (esp_now_add_peer(&peerInfo) != ESP_OK){
    Serial.println("Failed to add peer");
    return;
  }
  // Register for a callback function that will be called when data is received
  esp_now_register_recv_cb(OnDataRecv);
  Serial.println("ESP_NOW initialized");
}

// Estimate of a torque map
float torque_map(float w_input, int8_t gear, float w_min, float w_mid, float w_cutoff, float w_max, float T_max){
  float T_out;

  if (gear == 0){
    return 0;
  }

  if (gear == 1){
    w_min = 0;
    w_mid = 0;
  }

  w_input /= GEAR_RATIOS[gear + 1];

  if (w_input < w_min){ // Low rpm, output low torque
    T_out = 0.1*T_max;
  }else if (w_input < w_mid){ // Mid rpm, increase linearly
    T_out = T_max * (w_input - w_min) / (w_mid - w_min);
  }else if (w_input < w_cutoff){ // Optimal rpm, constant output
    T_out = T_max;
  }else if (w_input < w_max){ // Increasing rpm, decrease torque linearly
    T_out = T_max * (1 - (w_input - w_cutoff) / (w_max - w_cutoff));
  }else{ // Too high rpm, output low torque
    T_out = 0.05*T_max;
  }
  
  // Torque scaling based on gear
  T_out *= GEAR_RATIOS[gear + 1];

  return T_out;
}

// The task that finally applies new motor voltages and servo position
void motor_task(void *pvParameter){

  TickType_t xLastWakeTime;
  const TickType_t xFrequency = pdMS_TO_TICKS(1000.0 / MOTOR_TASK_FREQ);
  BaseType_t xWasDelayed;
  // Initialise the xLastWakeTime variable with the current time.
  xLastWakeTime = xTaskGetTickCount();

  while(1){
    // Wait for the next cycle.
    xWasDelayed = xTaskDelayUntil( &xLastWakeTime, xFrequency );
    // xWasDelayed value can be used to determine whether a deadline was missed
    // if the code here took too long.
    
    wheel_throttle = incoming_message.throttle;
    wheel_brake = incoming_message.brake;
    wheel_angle = incoming_message.angle;
    current_gear = incoming_message.gear;

    wheel_throttle *= torque_map(m_meas[0].w_m, current_gear, 2, 5, 10, 15, 1);

    servo.write(int(90 - constrain(wheel_angle * 50.0/90.0, -50.0, 50.0)));
  
    if(wheel_throttle > 0){
      // Temp
      ledcWrite(M2_ASS_PWM_CHL, wheel_throttle*POWER_SCALING);
      ledcWrite(M3_ASS_PWM_CHL, wheel_throttle*POWER_SCALING);
    }
    else{
      ledcWrite(M2_ASS_PWM_CHL, 0);
      ledcWrite(M3_ASS_PWM_CHL, 0);
    }

    if(wheel_brake > 0){
      // Temp
      ledcWrite(M1_ASS_PWM_CHL, wheel_brake*POWER_SCALING);
      ledcWrite(M0_ASS_PWM_CHL, wheel_brake*POWER_SCALING);
    }
    else{
      ledcWrite(M1_ASS_PWM_CHL, 0);
      ledcWrite(M0_ASS_PWM_CHL, 0);
    }
  }

}



// A peripheral task
void peripheral_task(void *pvParameter){

  TickType_t xLastWakeTime;
  const TickType_t xFrequency = pdMS_TO_TICKS(1000.0 / PERIPH_TASK_FREQ);
  BaseType_t xWasDelayed;
  // Initialise the xLastWakeTime variable with the current time.
  xLastWakeTime = xTaskGetTickCount();

  float pitch;

  float w_out;

  while(1){
    // Wait for the next cycle.
    xWasDelayed = xTaskDelayUntil( &xLastWakeTime, xFrequency );
    // xWasDelayed value can be used to determine whether a deadline was missed
    // if the code here took too long.
    
    pitch = 500 + 500 * GEAR_RATIOS[current_gear + 1] * m_meas[0].w_m / 30.0;
    // pitch = 500 + 500 * current_gear;

    buzz_hz(pitch);
    
    imu_LSM6D.update();

    
    // buzz_hz(500 + 100 * outgoing_message.w_ICE / 30.0);
    
    if(current_gear == 0){
      w_out = 0;
    }else{
      w_out = m_meas[0].w_m / GEAR_RATIOS[current_gear + 1];
    }

    outgoing_message.w_ICE = w_out;
    outgoing_message.phi = m_meas[0].phi;
    outgoing_message.hall = wheel_throttle;
    esp_err_t result = esp_now_send(wheel_address, (uint8_t *) &outgoing_message, sizeof(outgoing_message));
  }
}


// The task that measures wheel speed
void speed_measurement_task(void *pvParameter){

  TickType_t xLastWakeTime;
  const TickType_t xFrequency = pdMS_TO_TICKS(1000.0 / SPEED_TASK_FREQ);
  BaseType_t xWasDelayed;
  // Initialise the xLastWakeTime variable with the current time.
  xLastWakeTime = xTaskGetTickCount();

  float angle;

  float alpha_hall = 1;

  float alpha = 1;

  // float max_w_change = 0.5;

  for (int i = 0; i < 4; i++){
    m_meas[i].min = 600;
    m_meas[i].max = 800;
  }

  while(1){
    // Wait for the next cycle.
    xWasDelayed = xTaskDelayUntil( &xLastWakeTime, xFrequency );
    // xWasDelayed value can be used to determine whether a deadline was missed
    // if the code here took too long.

    // Filter hall-effect signal
    m_meas[0].hall_val = analogRead(HALL_EFF_0_PIN) * alpha_hall + (1.0 - alpha_hall) * m_meas[0].hall_val;

    // Update if new max/min has been measured
    if (m_meas[0].hall_val > m_meas[0].max){
      m_meas[0].max = m_meas[0].hall_val;
      m_meas[0].mid = (m_meas[0].max + m_meas[0].min) / 2.0;
    }
    else if(m_meas[0].hall_val < m_meas[0].min){
      m_meas[0].min = m_meas[0].hall_val;
      m_meas[0].mid = (m_meas[0].max + m_meas[0].min) / 2.0;
    }

    m_meas[0].phi_last = m_meas[0].phi;
    // Convert to sine wave with amplitude 1, and extract angle from arcsin()
    m_meas[0].phi = asin((float)(m_meas[0].hall_val - m_meas[0].mid) / ((float)m_meas[0].max - m_meas[0].mid));

    m_meas[0].w_stored.push_front(m_meas[0].w_m);
    m_meas[0].w_stored.pop_back();
    // (Angle - old_angle) / T
    m_meas[0].w_m = (float)(abs(m_meas[0].phi - m_meas[0].phi_last)) / (float)(1.0/SPEED_TASK_FREQ);

    // m_meas[0].w_m = constrain(m_meas[0].w_m, m_meas[0].w_last - max_w_change, m_meas[0].w_last + max_w_change);

    // m_meas[0].w_m = abs(m_meas[0].w_m);

    //m_meas[0].w_m = alpha * m_meas[0].w_m + (1.0-alpha) * m_meas[0].w_stored.back();

    // Average over recent values
    m_meas[0].w_m = (1.0 / (num_old_w_samples + 1)) * (m_meas[0].w_m + std::accumulate(m_meas[0].w_stored.begin(), m_meas[0].w_stored.end(), 0));
  }
}


// Motor_controller motor_controller = Motor_controller();

void init_i2c(){
  Wire.setPins(SDA, SCL);
  Wire.begin();
}

void init_tasks(){
  xTaskCreatePinnedToCore(motor_task, "motor_task", 2048, NULL, 1, NULL, MOTOR_TASK_CORE);
  xTaskCreatePinnedToCore(peripheral_task, "peripheral_task", 2048, NULL, 1, NULL, PERIPH_TASK_CORE);
  xTaskCreatePinnedToCore(speed_measurement_task, "speed_measurement_task", 2048, NULL, 1, NULL, SPEED_TASK_CORE);
}

void init_pins(){
  // Motors
  pinMode(M0_FWR_PIN, OUTPUT);
  pinMode(M0_REV_PIN, OUTPUT);
  pinMode(M1_FWR_PIN, OUTPUT);
  pinMode(M1_REV_PIN, OUTPUT);
  pinMode(M2_FWR_PIN, OUTPUT);
  pinMode(M2_REV_PIN, OUTPUT);
  pinMode(M3_FWR_PIN, OUTPUT);
  pinMode(M3_REV_PIN, OUTPUT);

  digitalWrite(M0_FWR_PIN, 0);
  digitalWrite(M0_REV_PIN, 0);
  digitalWrite(M1_FWR_PIN, 0);
  digitalWrite(M1_REV_PIN, 0);
  digitalWrite(M2_FWR_PIN, 0);
  digitalWrite(M2_REV_PIN, 0);
  digitalWrite(M3_FWR_PIN, 0);
  digitalWrite(M3_REV_PIN, 0);

  // Motor directions
  pinMode(M0_DIR_PIN, OUTPUT);
  pinMode(M1_DIR_PIN, OUTPUT);
  pinMode(M2_DIR_PIN, OUTPUT);
  pinMode(M3_DIR_PIN, OUTPUT);

  digitalWrite(M0_DIR_PIN, 1);
  digitalWrite(M1_DIR_PIN, 0);
  digitalWrite(M2_DIR_PIN, 0);
  digitalWrite(M3_DIR_PIN, 0);

  // Buzzer
  ledcAttachPin(BUZZER_PIN, BUZZER_CHNL);
}

void init_motors(){
  ledcDetachPin(M1_FWR_PIN);
  ledcDetachPin(M1_REV_PIN);
  ledcDetachPin(M2_FWR_PIN);
  ledcDetachPin(M2_REV_PIN);
  ledcDetachPin(M3_FWR_PIN);
  ledcDetachPin(M3_REV_PIN);
  ledcDetachPin(M0_FWR_PIN);
  ledcDetachPin(M0_REV_PIN);

  delay(500);

  digitalWrite(M0_REV_PIN, 0);
  ledcSetup(M0_ASS_PWM_CHL, MOTOR_PWM_FREQ, MOTOR_PWM_BIT_RES);
  ledcAttachPin(M0_FWR_PIN, M0_ASS_PWM_CHL);
  
  digitalWrite(M1_FWR_PIN, 0);
  ledcSetup(M1_ASS_PWM_CHL, MOTOR_PWM_FREQ, MOTOR_PWM_BIT_RES);
  ledcAttachPin(M1_REV_PIN, M1_ASS_PWM_CHL);

  digitalWrite(M2_REV_PIN, 0);
  ledcSetup(M2_ASS_PWM_CHL, MOTOR_PWM_FREQ, MOTOR_PWM_BIT_RES);
  ledcAttachPin(M2_FWR_PIN, M2_ASS_PWM_CHL);
  
  digitalWrite(M3_FWR_PIN, 0);
  ledcSetup(M3_ASS_PWM_CHL, MOTOR_PWM_FREQ, MOTOR_PWM_BIT_RES);
  ledcAttachPin(M3_REV_PIN, M3_ASS_PWM_CHL);


  ledcWrite(M0_FWR_PIN, 0);
  ledcWrite(M1_FWR_PIN, 0);
  ledcWrite(M2_FWR_PIN, 0);
  ledcWrite(M3_FWR_PIN, 0);

  m_meas[0].pin = HALL_EFF_0_PIN;
  m_meas[1].pin = HALL_EFF_1_PIN;
  m_meas[2].pin = HALL_EFF_2_PIN;
  m_meas[3].pin = HALL_EFF_3_PIN;

  for (int i = 0; i < 4; i++){
    m_meas[i].max = 1500;
    m_meas[i].min = 150;
    m_meas[i].mid = (m_meas[i].max + m_meas[i].min) / 2;
  }

  delay(250);
}

uint8_t servo_channel;

void setup() {
  // Serial.begin(115200);
  Serial.println("Car started");

  servo.setPeriodHertz(50);
	servo_channel = servo.attach(SERVO_PIN, 925, 1925);
  servo.write(90);

  init_pins();
  init_i2c();
  imu_LSM6D.begin();

  delay(1000);

  init_esp_now();

  //Serial.println("Program started");
  // Serial.println("Servo channel: "+String(servo_channel));

  //motor_controller.begin();

  init_motors();

  // buzz_hz(0);
  // ledcChangeFrequency(BUZZER_CHNL, 0, 8);
  // ledcWrite(BUZZER_CHNL, 50);
  // while(1){
  //   for(int i = 0; i < 10000; i += 10){
  //     ledcChangeFrequency(BUZZER_CHNL, i, 8);
  //     delay(7);
  //   }

  // }


  // Start the tasks
  init_tasks();

}

void loop() {

  while(1){
    vTaskDelay(1000000 / portTICK_RATE_MS);
  }



  // int channel1 = M1_ASS_PWM_CHL;
  // int channel2 = M2_ASS_PWM_CHL;
  // int channel3 = M3_ASS_PWM_CHL;
  // int channel4 = M0_ASS_PWM_CHL;
  
  
  
  // Serial.println("T > 0");
  // ledcWrite(channel1, 50);
  // ledcWrite(channel2, 50);
  // delay(2000);
  // Serial.println("T = 0\n");
  // ledcWrite(channel1, 0);
  // ledcWrite(channel2, 0);
  // delay(2000);

  // Serial.println(String(wheel_throttle)+" "+String(wheel_brake)+" "+String(wheel_angle)+"\n");
  // Serial.println(90 + constrain(wheel_angle * 50.0/90.0, -50.0, 50.0));
  // Serial.flush();


  // while(1){
  //   //Serial.println("T > 0");
  //   ledcWrite(channel1, 100);
  //   delay(10);
  //   ledcWrite(channel2, 100);
  //   delay(10);
  //   ledcWrite(channel3, 100);
  //   delay(10);
  //   ledcWrite(channel4, 100);
  //   delay(2000);
  //   //Serial.println("T = 0\n");
  //   ledcWrite(channel1, 0);
  //   delay(10);
  //   ledcWrite(channel2, 0);
  //   delay(10);
  //   ledcWrite(channel3, 0);
  //   delay(10);
  //   ledcWrite(channel4, 0);
  //   delay(4000);

  }
  










  // ledcWrite(M1_ASS_PWM_CHL, 10);
  // delay(10);
  // ledcWrite(M2_ASS_PWM_CHL, 10);
  // delay(10);
  // // ledcWrite(M3_ASS_PWM_CHL, 10);
  // delay(10);
  // ledcWrite(M4_ASS_PWM_CHL, 10);

  // delay(500);

  // // ledcWrite(M1_ASS_PWM_CHL, 0);
  // delay(10);
  // ledcWrite(M2_ASS_PWM_CHL, 0);
  // delay(10);
  // // ledcWrite(M3_ASS_PWM_CHL, 0);
  // delay(10);
  // ledcWrite(M4_ASS_PWM_CHL, 0);
  // delay(3000);

  // // ledcDetachPin(M1_FWR_PIN);
  // // delay(10);
  // // digitalWrite(M1_FWR_PIN, 0);
  // // delay(10);
  // // ledcSetup(M1_ASS_PWM_CHL, MOTOR_PWM_FREQ, MOTOR_PWM_BIT_RES);
  // // delay(10);
  // // ledcAttachPin(M1_REV_PIN, M1_ASS_PWM_CHL);

  // delay(10);
  // ledcDetachPin(M2_FWR_PIN);
  // // ledcDetachPin(M2_REV_PIN);
  // delay(10);
  // pinMode(M2_FWR_PIN, OUTPUT);
  // digitalWrite(M2_FWR_PIN, 0);
  // delay(10);
  // // ledcSetup(M2_ASS_PWM_CHL, MOTOR_PWM_FREQ, MOTOR_PWM_BIT_RES);
  // delay(10);
  // ledcAttachPin(M2_REV_PIN, M2_ASS_PWM_CHL);
  
  // // delay(10);
  // // ledcDetachPin(M3_FWR_PIN);
  // // delay(10);
  // // digitalWrite(M3_FWR_PIN, 0);
  // // delay(10);
  // // // ledcSetup(M3_ASS_PWM_CHL, MOTOR_PWM_FREQ, MOTOR_PWM_BIT_RES);
  // // delay(10);
  // // ledcAttachPin(M3_REV_PIN, M3_ASS_PWM_CHL);

  // delay(10);
  // ledcDetachPin(M4_FWR_PIN);
  // // ledcDetachPin(M4_REV_PIN);
  // delay(10);
  // digitalWrite(M4_FWR_PIN, 0);
  // delay(10);
  // // ledcSetup(M4_ASS_PWM_CHL, MOTOR_PWM_FREQ, MOTOR_PWM_BIT_RES);
  // delay(10);
  // ledcAttachPin(M4_REV_PIN, M4_ASS_PWM_CHL);
  // delay(10);
  

  // // ledcWrite(M1_ASS_PWM_CHL, 10);
  // delay(10);
  // ledcWrite(M2_ASS_PWM_CHL, 10);
  // delay(10);
  // // ledcWrite(M3_ASS_PWM_CHL, 10);
  // delay(10);
  // ledcWrite(M4_ASS_PWM_CHL, 10);
  // delay(500);
  // // ledcWrite(M1_ASS_PWM_CHL, 0);
  // ledcWrite(M2_ASS_PWM_CHL, 0);
  // // ledcWrite(M3_ASS_PWM_CHL, 0);
  // ledcWrite(M4_ASS_PWM_CHL, 0);
  // delay(4000);

  // // ledcDetachPin(M1_REV_PIN);
  // // delay(10);
  // // digitalWrite(M1_REV_PIN, 0);
  // // delay(10);
  // // // ledcSetup(M1_ASS_PWM_CHL, MOTOR_PWM_FREQ, MOTOR_PWM_BIT_RES);
  // // delay(10);
  // // ledcAttachPin(M1_FWR_PIN, M1_ASS_PWM_CHL);
  // // delay(10);

  // ledcDetachPin(M2_REV_PIN);
  // // ledcDetachPin(M2_FWR_PIN);
  // delay(10);
  // digitalWrite(M2_REV_PIN, 0);
  // delay(10);
  // // ledcSetup(M2_ASS_PWM_CHL, MOTOR_PWM_FREQ, MOTOR_PWM_BIT_RES);
  // delay(10);
  // ledcAttachPin(M2_FWR_PIN, M2_ASS_PWM_CHL);
  // delay(10);
  
  // // ledcDetachPin(M3_REV_PIN);
  // // delay(10); 
  // // digitalWrite(M3_REV_PIN, 0);
  // // delay(10);
  // // // ledcSetup(M3_ASS_PWM_CHL, MOTOR_PWM_FREQ, MOTOR_PWM_BIT_RES);
  // // delay(10);
  // // ledcAttachPin(M3_FWR_PIN, M3_ASS_PWM_CHL);
  // // delay(10);

  // ledcDetachPin(M4_REV_PIN);
  // // ledcDetachPin(M4_FWR_PIN);
  // delay(10);
  // digitalWrite(M4_REV_PIN, 0);
  // delay(10);
  // // ledcSetup(M4_ASS_PWM_CHL, MOTOR_PWM_FREQ, MOTOR_PWM_BIT_RES);
  // delay(10);
  // ledcAttachPin(M4_FWR_PIN, M4_ASS_PWM_CHL);

  // delay(10);
  // motor_controller.forward(0,1);
  // motor_controller.forward(1,1);
  // motor_controller.forward(2,1);
  // motor_controller.forward(3,1);
  
  // delay(4000);

  // motor_controller.forward(0,0);
  // motor_controller.forward(1,0);
  // motor_controller.forward(2,0);
  // motor_controller.forward(3,0);


  // delay(4000);

  
  // motor_controller.reverse(0,1);
  // motor_controller.reverse(1,1);
  // motor_controller.reverse(2,1);
  // motor_controller.reverse(3,1);
  
  // delay(4000);

  // motor_controller.reverse(0,0);
  // motor_controller.reverse(1,0);
  // motor_controller.reverse(2,0);
  // motor_controller.reverse(3,0);


  // delay(4000);
  

// ------------------------------- MAC ADDRESS ---------------------------

// #include <Wire.h>

// #ifdef ESP32
//   #include <WiFi.h>
// #else
//   #include <ESP8266WiFi.h>
// #endif

// void setup(){
//   Serial.begin(115200);
//   Serial.println();
//   delay(2000);
//   Serial.print("ESP Board MAC Address:  ");
//   Serial.println(WiFi.macAddress());
// }
 
// void loop(){

// }


// // I2C address scanner program
// #include <Wire.h>
// #include <Arduino.h>

// void setup()
// {
//   Wire.setPins(8,9);
//   Wire.begin();
//   Serial.begin(115200);
//   Serial.println("I2C Scanner");

// }

// void loop()
// {
//   byte error, address;
//   int nDevices;

//   Serial.println("Scanning...");

//   nDevices = 0;
//   for(address = 1; address < 127; address++ )
//   {
//     Wire.beginTransmission(address);
//     error = Wire.endTransmission();

//     if (error == 0)
//     {
//       Serial.print("I2C device found at address 0x");
//       if (address < 16)
//         Serial.print("0");

//       Serial.print(address,HEX);
//       Serial.println("  !");

//       nDevices++;
//     }
//     else if (error==4)
//     {
//       Serial.print("Unknown error at address 0x");
//       if (address < 16)
//         Serial.print("0");

//       Serial.println(address,HEX);
//     }
//   }

//   if (nDevices == 0)
//     Serial.println("No I2C devices found");
//   else
//     Serial.println("done");

//   delay(5000); // wait 5 seconds for next scan
// }

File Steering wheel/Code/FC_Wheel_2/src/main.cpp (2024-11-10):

#include <Arduino.h>
#include <Wire.h>
#include <SPI.h>
#include <TFT_eSPI.h> // Main library used
#include <Wire.h>

#include <numeric>
#include <vector>

// RPM LED strip
#include "TLC_LED_Array.h"

// For the TFT SPI 240*320 display
#include "FC_Display.h"

// Global variables and definitions
#include "Global_Variables.h"

// Functions for all the peripherals
#include "Peripheral_Functions.h"

// MPU6050 IMU
#include <MPU6050_tockn.h>

#include "esp_now.h"
#include "Wifi.h"

// Wheel 2.0 MAC: 34:85:18:5C:86:A0
uint8_t wheel_address[] = {0x34, 0x85, 0x18, 0x5C, 0x86, 0xA0};

// Car MAC: 0x34, 0x85, 0x18, 0x89, 0xE0, 0xA8
uint8_t car_address[] = {0x34, 0x85, 0x18, 0x89, 0xE0, 0xA8};

typedef struct wheel_to_car_msg {
    uint8_t throttle;
    uint8_t brake;
    float angle;
    int8_t gear;
} wheel_to_car_msg;

typedef struct car_to_wheel_msg {
    float w_ICE;
    float phi; // rad
    float hall;
} car_to_wheel_msg;


car_to_wheel_msg incoming_message;

wheel_to_car_msg outgoing_message;

esp_now_peer_info_t peerInfo;
String success;
bool espnow_connected = false;
// Callback when data is sent
void OnDataSent(const uint8_t *mac_addr, esp_now_send_status_t status) {
  // Serial.print("\r\nLast Packet Send Status:\t");
  // Serial.println(status == ESP_NOW_SEND_SUCCESS ? "Delivery Success" : "Delivery Fail");
  
  if (status == 0){
    espnow_connected = true;
    success = "Delivery Success :)";
  }
  else{
    espnow_connected = false;
    success = "Delivery Fail :(";
  }
}

uint8_t wheel_throttle;
uint8_t wheel_brake;
float wheel_angle_deg;

// Callback when data is received
void OnDataRecv(const uint8_t * mac, const uint8_t *incomingData, int len) {
  memcpy(&incoming_message, incomingData, sizeof(incoming_message));
  //Serial.print("Bytes received: ");
  //Serial.println(len);
}
  

void init_esp_now(){
  // Set device as a Wi-Fi Station
  WiFi.mode(WIFI_STA);

  // Init ESP-NOW
  if (esp_now_init() != ESP_OK) {
    Serial.println("Error initializing ESP-NOW");
    return;
  }

  // Once ESPNow is successfully Init, we will register for Send CB to
  // get the status of Trasnmitted packet
  esp_now_register_send_cb(OnDataSent);
  
  // Register peer
  memcpy(peerInfo.peer_addr, car_address, 6);
  peerInfo.channel = 0;  
  peerInfo.encrypt = false;
  
  // Add peer        
  if (esp_now_add_peer(&peerInfo) != ESP_OK){
    Serial.println("Failed to add peer");
    return;
  }
  // Register for a callback function that will be called when data is received
  esp_now_register_recv_cb(OnDataRecv);
  Serial.println("ESP_NOW initialized");
}


void buzz1(uint16_t freq){
  ledcWriteTone(BZR_1_CHANNEL, freq);
}

void buzz2(uint16_t freq){
  ledcWriteTone(BZR_2_CHANNEL, freq);
}

void setup_pins(){
  pinMode(BAT_LEVEL_PIN, INPUT);
  pinMode(VOLUME_PIN, INPUT);

  pinMode(BTN1_PIN, INPUT_PULLDOWN);
  pinMode(BTN2_PIN, INPUT_PULLDOWN);
  pinMode(BTN3_PIN, INPUT_PULLDOWN);
  pinMode(BTN4_PIN, INPUT_PULLDOWN);
  
  pinMode(L_TRIGGER_PIN, INPUT);
  pinMode(R_TRIGGER_PIN, INPUT);

  ledcAttachPin(BUZZ_1_PIN, BZR_1_CHANNEL);
  ledcAttachPin(BUZZ_2_PIN, BZR_2_CHANNEL);

  pinMode(L_PADDLE_PIN, INPUT_PULLDOWN);
  pinMode(R_PADDLE_PIN, INPUT_PULLDOWN);
}

void beep_beep(){
  buzz1(1000);
  delay(100);
  buzz1(0);
  delay(50);
  buzz2(1000);
  delay(100);
  buzz2(0);
}

int16_t low_pass_filter(int16_t new_val, int16_t old_val, float alpha){
  return alpha * new_val + (1 - alpha) * old_val;
}

float read_battery_voltage(){
  return battery_voltage_coeff * analogRead(BAT_LEVEL_PIN);
}

/* Filter the raw data from digital input
@param input Address to an 'Input_Peripheral'
*/
template <typename Func>
void debounce_input(Peripheral_Digital<Func>* input){
  // New value detected, init debouncing
    if((input->raw_val != input->current_val) && !input->debounce_state){
      //Serial.println("Debounce started, old: " + String(input->current_val) + 
      //        " new: " + String(input->raw_val));
      input->current_val = input->raw_val; // Immediately update the value in use

      // Call the assigned function to that specific input and send in the current state
      input->assigned_function(input->current_val);

      input->debounce_state = true;
      input->input_streak = 1;
    }else if(input->debounce_state){
      // If enough samples are identical in a row, assume bouncing has settled
      if (input->input_streak >= PADDLE_DEBOUNCE_STREAK){
        //Serial.println("Debounce ended, new: "+String(input->raw_val)+
        //      ", num_same = "+String(input->input_streak)+"\n\n");
        input->debounce_state = false;
        input->input_streak = 0;
      }
      // Count streak of the same value during debouncing
      else if (input->raw_val == input->last_val) {
        input->input_streak++;
      }
      else {
        input->input_streak = 1;
      }
      //Serial.println("Num same: " + String(input->input_streak));
    }

    input->last_val = input->raw_val;
}


// The task that handles reading digital inputs
void button_task(void *pvParameter){

  TickType_t xLastWakeTime;
  const TickType_t xFrequency = pdMS_TO_TICKS(1000.0 / BUTTON_TASK_FREQ);
  BaseType_t xWasDelayed;
  // Initialise the xLastWakeTime variable with the current time.
  xLastWakeTime = xTaskGetTickCount();
  bool debounce_paddle_R = false;
  bool last_paddle_R = false;
  uint16_t num_same_paddle_R = 1;

  bool debounce_paddle_L = false;
  uint16_t num_same_paddle_L = 1;

  while(1){
    // Wait for the next cycle.
    xWasDelayed = xTaskDelayUntil( &xLastWakeTime, xFrequency );
    // xWasDelayed value can be used to determine whether a deadline was missed
    // if the code here took too long.
    
    Paddle_R.raw_val = digitalRead(R_PADDLE_PIN);
    Paddle_L.raw_val = digitalRead(L_PADDLE_PIN);

    //disp.battery_SoC(read_battery_voltage());

    debounce_input(&Paddle_R);
    debounce_input(&Paddle_L);
  }
}
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

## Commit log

2023-01-17 Init component research
    [Motor specs.xlsx]
2023-01-18 Add outrunner tyre prototype STL
    [Back wheel outrunner on motor 2.stl, UM3E_Back wheel outrunner on motor 2.3mf]
2023-01-25 Begin PCB
    [FC Control board 1.0.kicad_pcb, FC Control board 1.0.kicad_sch]
2023-01-28 Prototype 2
    [Back wheel v1.stl, FC_Prototype2.3mf, Frame V2.stl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]
2023-01-29 Begin electric motor control design
    [FC Control board 1.0.kicad_sch]
2023-03-19 Continue PCB-design
    [FC Control board 1.0.kicad_pcb, FC Control board 1.0.kicad_sch, PCB-outline.dxf]
2023-09-02 Restart project
    [FC Control board 1.0.kicad_pcb, FC Control board 1.0.kicad_sch, PCB-outline.dxf]
2023-09-22 Add pictures
    [Motor specs.xlsx]
2023-09-23 Add dash display demo
    [Front dash v21.stl, PCB_outline_prototype4.dxf]
2023-10-02 Add stl-files
    [Back plate.stl, LeftBackHandle.stl, LeftFrontHandle.stl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]
2023-10-04 Add stl
    [Back plate.stl, Front dash v21.stl, LeftBackHandle.stl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]
2023-10-06 FC control board V1.0
    As ordered from JLC
    [FC Control board 1.0-B_Cu.gbl, FC Control board 1.0-B_Mask.gbs, FC Control board 1.0-B_Paste.gbp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]
2023-10-06 First wireless test
2023-10-06 Moved files
    [FC Control board 1.0-B_Cu.gbl, FC Control board 1.0-B_Mask.gbs, FC Control board 1.0-B_Paste.gbp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]
2023-10-06 Added PCB media
2023-10-07 Wheel PCB 1.0
    [Back plate.stl, FC_Wheel_PCB.kicad_pcb, FC_Wheel_PCB.kicad_sch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]
2023-10-07 Finish up wheel PCB
    [Back plate v36.stl, FC_Wheel_PCB.kicad_pcb, FC_Wheel_PCB.kicad_sch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]
2023-10-07 Polish Wheel PCB [ Ordered ]
    [16_Channel_LED_Strip.kicad_pcb, 16_Channel_LED_Strip.kicad_sch, Cover v40.stl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]
2023-10-08 Init LED controller PCB
    [16_Channel_LED_Strip.kicad_pcb, 16_Channel_LED_Strip.kicad_sch, Battery Lid.stl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]
2023-10-18 Simple analog test, ex. for hall sensor
    [data.csv, video_data.csv]
2023-10-18 Start of code for FC-control-board
2023-10-19 Finish LED PCB [Ordered]
    [16_Channel_LED_Strip-B_Cu.gbr, 16_Channel_LED_Strip-B_Mask.gbr, 16_Channel_LED_Strip-B_Paste.gbr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]
2023-10-22 FC control board v1.1 [Ordered]
    [FC Control board 1.1-B_Cu.gbl, FC Control board 1.1-B_Mask.gbs, FC Control board 1.1-B_Paste.gbp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]
2023-11-04 Sync old files
    [Bolt_plug.stl, Handle_back_R.stl, Handle_front_R.stl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]
2023-11-04 Sync old files #2
    [16_Channel_LED_Strip.step, FC_Wheel_PCB-2.0.kicad_pcb, FC_Wheel_PCB-2.0.kicad_sch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]
2023-11-04 Add successful TFT-display demo with ESP32-S3
    ESP32-S2 worked fine, S3 took some time. Note 'platformio.ini' with USB flags. New library for the TFT display
2023-11-05 Implement gear shifter demo on S3
2023-11-05 Stable TFT (THT_RST to GPIO fix)
    [main.cpp]
2023-11-06 FC_Wheel_PCB 2.0 [Ordered]
    [FC_Wheel_PCB-2.0-B_Cu.gbr, FC_Wheel_PCB-2.0-B_Mask.gbr, FC_Wheel_PCB-2.0-B_Paste.gbr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]
2023-11-07 Implement functional RPM LED array
2023-11-11 Fancy but buggy 'ramp_set()'
    [main.cpp]
2023-11-23 Add code to PCB 2.0
    [Battery Lid v2.stl, Camera mount TX06_-2deg.stl, Camera mount TX06_-5deg.stl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]
2023-11-24 Add gear shifting and throttle demo
2023-11-26 Add and fix .gitignore
    [FC Control board 1.2.csv, FC Control board 1.2.kicad_pcb, FC Control board 1.2.kicad_sch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]
2023-11-26 Implement stable gear shifting with better structure
    [Battery Lid v2.stl]
2023-11-28 Add throttle and braking measurement with basic filters
2023-11-30 Begin IMU class
2023-12-02 Angle from IMU, throttle bar, braking bar
2023-12-06 First Formula-CASE car tested
2023-12-07 Continue PWM debugging
2023-12-09 Begin FC Control Board 1.3
    [FC Control board 1.2.csv, FC Control board 1.3.kicad_pcb, FC Control board 1.3.kicad_sch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]
2023-12-10 Continue FC 1.3
    [FC Control board 1.3.kicad_pcb, FC Control board 1.3.kicad_sch]
2023-12-11 FC 1.3 -> FC 2.0
    [FC Control board 1.2.csv, FC Control board 1.3.kicad_pcb, FC Control board 2.0.kicad_pcb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]
2023-12-12 Functioning 1.2 prototype
    [FC Control board 2.0.kicad_sch]
2023-12-20 Add clamping diodes and opto couplers
    [FC Control board 2.0.kicad_pcb, FC Control board 2.0.kicad_sch]
2024-01-02 Final version of 2.0 [Ordered]
    [FC Control board 2.0.kicad_pcb, FC Control board 2.0.kicad_sch]
2024-01-28 Add .stl for v35
    [Battery Lid v2.stl, Camera mount TX06_-2.stl, Frame.stl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]
2024-03-02 Implement IMU functionality
    [Battery Lid v2.stl, Frame.stl, Front wing.stl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]
2024-03-02 Add sensor calibration MATLAB script
2024-03-11 Fix sensor resolution, fix noise statistics
    [main.cpp]
2024-03-24 Hall sensor notes

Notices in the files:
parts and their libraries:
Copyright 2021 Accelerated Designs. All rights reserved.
